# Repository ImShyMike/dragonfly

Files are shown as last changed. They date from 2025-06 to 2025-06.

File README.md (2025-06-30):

# dragonfly

A tiny 3.5" FPV drone for [highway](https://highway.hackclub.com) with a fully custom frame, corners, softmounts and ELRS receiver.

I've seen many FPV videos and always thought that it was really cool. Only issue is that I only own a small toy drone without a camera.

When highway released I thought it would be a great oportunity to learn what goes into designing your own FPV drone. After alot of research I managed to make a decent looking frame and find parts that could keep the cost reasonably low.

---

## Render

Model render

<sub>The model with sample props, motors and camera (along with a 15cm ruler for scale).</sub>

Custom ELRS PCB render

---

## BOM

| Part | Qty | Price (USD) | Link |
| --- | :-: | :---: | --- |
| SpeedyBee F405 Mini BLS 35A 20×20 Stack  |  1  | 60.00 | [https://www.speedybee.com/speedybee-f405-mini-bls-35a-20x20-stack](https://www.speedybee.com/speedybee-f405-mini-bls-35a-20x20-stack) |
| 20 mm Aluminum Standoffs (pack) |  1  | 1.86 | [https://pt.aliexpress.com/item/1005007945167923.html](https://pt.aliexpress.com/item/1005007945167923.html) |
| HQProp 3525 Prop Set |  1  | 3.31 | [https://pt.aliexpress.com/item/1005008744409414.html](https://pt.aliexpress.com/item/1005008744409414.html) |
| CADDX ANT Camera |  1  | 13.98 | [https://pt.aliexpress.com/item/1005006086694992.html](https://pt.aliexpress.com/item/1005006086694992.html) |
| Omnidirectional Antenna Pair |  1  | 2.46 | [https://pt.aliexpress.com/item/1005007126266614.html](https://pt.aliexpress.com/item/1005007126266614.html) |
| YSIDO 1505 2650KV Brushless Motor Set |  1  | 29.11 | [https://pt.aliexpress.com/item/1005007544080274.html](https://pt.aliexpress.com/item/1005007544080274.html) |
| HGLRC Zeus Nano VTX |  1  | 22.96 | [https://pt.aliexpress.com/item/1005008043478143.html](https://pt.aliexpress.com/item/1005008043478143.html) |
| Mini RHCP 5.8 GHz Lollipop Antenna (UFL) |  1  | 5.34 | [https://pt.aliexpress.com/item/4001365632031.html](https://pt.aliexpress.com/item/4001365632031.html) |
| **Total** | |  **139.02** | |

The current price of the ELRS receiver is 69.60$ and using the cheapest shipping the total is at 215.91$.

The BOM does not account for the frame and battery as I couldn't get that under 150$ D:

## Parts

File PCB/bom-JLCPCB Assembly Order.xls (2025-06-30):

JLCPCB BOM Tool - BOM Matching
BOM name：bom-JLCPCB Assembly Order.xlsx |  |  | Download Time：2025-06-25 01:11:42 |  |  |  | * Our matching results are updated in real-time, but stock and prices may change. If it's been over 24 hours, please re-match before placing your order.
PCB Assembled Qty：5 |  |  | Est. Total Price：20.4626
Your BOM |  |  |  |  | Matched Parts |  |  |  |  |  |  | Order Information
Top Designator | Bottom Designator | Comment | Footprint | JLCPCB Part # | Matches | Part # | Manufacturer | Footprint | Description | Category | Warning | JLCPCB Part # | Product link | Lib Type | Qty | Source | Total Price ($)
C1 |  | 25V1uF | 0402 |  | Unconfirmed | CL05A105KA5NQNC | Samsung Electro-Mechanics | 0402 | 25V 1uF X5R ±10% 0402 Multilayer Ceramic Capacitors MLCC - SMD/SMT ROHS | Multilayer Ceramic Capacitors MLCC - SMD/SMT | 1.The comment (CL05A105KA5NQNC) of this part does not match the one (25V1uF) provided in your BOM. Please confirm; 2.Multiple lines in the BOM have been matched to the same part. Please check if the matching is correct. ; | C52923 | https://jlcpcb.com/partdetail/53938-CL05A105KA5NQNC/C52923 | Basic | 6 | 6 JLCPCB | 0.018
C11 |  | 1uF25v | 0402 |  | Unconfirmed | CL05A105KA5NQNC | Samsung Electro-Mechanics | 0402 | 25V 1uF X5R ±10% 0402 Multilayer Ceramic Capacitors MLCC - SMD/SMT ROHS | Multilayer Ceramic Capacitors MLCC - SMD/SMT | 1.Multiple lines in the BOM have been matched to the same part. Please check if the matching is correct. ; | C52923 | https://jlcpcb.com/partdetail/53938-CL05A105KA5NQNC/C52923 | Basic | 6 | 6 JLCPCB | 0.018
C12 |  | 1uF | 0402 |  | Unconfirmed | CL05A105KA5NQNC | Samsung Electro-Mechanics | 0402 | 25V 1uF X5R ±10% 0402 Multilayer Ceramic Capacitors MLCC - SMD/SMT ROHS | Multilayer Ceramic Capacitors MLCC - SMD/SMT | 1.Multiple lines in the BOM have been matched to the same part. Please check if the matching is correct. ; | C52923 | https://jlcpcb.com/partdetail/53938-CL05A105KA5NQNC/C52923 | Basic | 6 | 6 JLCPCB | 0.018
C2 |  | 470nF,10V | 0402 |  | Select by System | CL05A474KP5NNNC | Samsung Electro-Mechanics | 0402 | 10V 470nF X5R ±10% 0402 Multilayer Ceramic Capacitors MLCC - SMD/SMT ROHS | Multilayer Ceramic Capacitors MLCC - SMD/SMT |  | C47339 | https://jlcpcb.com/partdetail/48344-CL05A474KP5NNNC/C47339 | Extended | 20 | 20 JLCPCB | 0.066
C3 |  | 10nF | 0402 |  | Select by System | CL05B103KB5NNNC | Samsung Electro-Mechanics | 0402 | 50V 10nF X7R ±10% 0402 Multilayer Ceramic Capacitors MLCC - SMD/SMT ROHS | Multilayer Ceramic Capacitors MLCC - SMD/SMT |  | C15195 | https://jlcpcb.com/partdetail/15869-CL05B103KB5NNNC/C15195 | Basic | 4 | 4 JLCPCB | 0.0052
C8 |  | 10nF | 0402 |  | Select by System | CL05B103KB5NNNC | Samsung Electro-Mechanics | 0402 | 50V 10nF X7R ±10% 0402 Multilayer Ceramic Capacitors MLCC - SMD/SMT ROHS | Multilayer Ceramic Capacitors MLCC - SMD/SMT |  | C15195 | https://jlcpcb.com/partdetail/15869-CL05B103KB5NNNC/C15195 | Basic | 4 | 4 JLCPCB | 0.0052
C4 |  | 10uF | 0402 |  | Select by System | CL05A106MQ5NUNC | Samsung Electro-Mechanics | 0402 | 6.3V 10uF X5R ±20% 0402 Multilayer Ceramic Capacitors MLCC - SMD/SMT ROHS | Multilayer Ceramic Capacitors MLCC - SMD/SMT |  | C15525 | https://jlcpcb.com/partdetail/16204-CL05A106MQ5NUNC/C15525 | Basic | 2 | 2 JLCPCB | 0.0122
C6,C7 |  | 10pF | 0402 |  | Select by System | CL05C100JB5NNNC | Samsung Electro-Mechanics | 0402 | 50V 10pF C0G ±5% 0402 Multilayer Ceramic Capacitors MLCC - SMD/SMT ROHS | Multilayer Ceramic Capacitors MLCC - SMD/SMT |  | C32949 | https://jlcpcb.com/partdetail/33914-CL05C100JB5NNNC/C32949 | Basic | 8 | 8 JLCPCB | 0.0344
C17,C19 |  | 10pF | 0402 |  | Select by System | CL05C100JB5NNNC | Samsung Electro-Mechanics | 0402 | 50V 10pF C0G ±5% 0402 Multilayer Ceramic Capacitors MLCC - SMD/SMT ROHS | Multilayer Ceramic Capacitors MLCC - SMD/SMT |  | C32949 | https://jlcpcb.com/partdetail/33914-CL05C100JB5NNNC/C32949 | Basic | 8 | 8 JLCPCB | 0.0344
C10,C5,C9 |  | 100nF | 0402 |  | Select by System | CL05B104KO5NNNC | Samsung Electro-Mechanics | 0402 | 16V 100nF X7R ±10% 0402 Multilayer Ceramic Capacitors MLCC - SMD/SMT ROHS | Multilayer Ceramic Capacitors MLCC - SMD/SMT |  | C1525 | https://jlcpcb.com/partdetail/1877-CL05B104KO5NNNC/C1525 | Basic | 8 | 8 JLCPCB | 0.0088
C18 |  | 100nF | 0402 |  | Select by System | CL05B104KO5NNNC | Samsung Electro-Mechanics | 0402 | 16V 100nF X7R ±10% 0402 Multilayer Ceramic Capacitors MLCC - SMD/SMT ROHS | Multilayer Ceramic Capacitors MLCC - SMD/SMT |  | C1525 | https://jlcpcb.com/partdetail/1877-CL05B104KO5NNNC/C1525 | Basic | 8 | 8 JLCPCB | 0.0088
C13 |  | 2.2uF | 0402 |  | Select by Customer | CL05A225MQ5NSNC | Samsung Electro-Mechanics | 0402 | 6.3V 2.2uF X5R ±20% 0402 Multilayer Ceramic Capacitors MLCC - SMD/SMT ROHS | Multilayer Ceramic Capacitors MLCC - SMD/SMT |  | C12530 | https://jlcpcb.com/partdetail/13164-CL05A225MQ5NSNC/C12530 | Basic | 2 | 2 JLCPCB | 0.0048
C14,C15,C16,C20 |  | 1.2pF | 0402 |  | Select by System | CC0402BRNPO9BN1R2 | YAGEO | 0402 | 50V 1.2pF NP0 0402 Multilayer Ceramic Capacitors MLCC - SMD/SMT ROHS | Multilayer Ceramic Capacitors MLCC - SMD/SMT |  | C327292 | https://jlcpcb.com/partdetail/YAGEO-CC0402BRNPO9BN1R2/C327292 | Extended | 20 | 20 JLCPCB | 0.044
CN1,CN2 |  | Conn_Coaxial | U.FL_Hirose_U.FL-R-SMT-1_Vertical |  | Select by System | U.FL-R-SMT-1(80) | HRS(Hirose) | SMD | 1 Inner pin IPEX Board-End 1.25mm -40℃~+90℃ 6GHz 50Ω 2mm SMD Coaxial Connectors (RF) ROHS | Coaxial Connectors (RF) |  | C88374 | https://jlcpcb.com/partdetail/HRS_Hirose-U_FL_R_SMT_1_80/C88374 | Extended | 6 | 6 JLCPCB | 0.5556
D1 |  | LED | 0603 |  | Select by System | KT-0603R | Hubei KENTO Elec | 0603 | -40℃~+85℃ Red 0603 LED Indication - Discrete ROHS | LED Indication - Discrete |  | C2286 | https://jlcpcb.com/partdetail/Hubei_KENTOElec-KT0603R/C2286 | Basic | 2 | 2 JLCPCB | 0.0112
L1 |  | 15u | 0805 |  | Select by System | MGFL2012F150MT-LF | microgate | 0805 | 400mA 15uH ±20% 500mΩ 0805 Inductors (SMD) ROHS | Inductors (SMD) |  | C486333 | https://jlcpcb.com/partdetail/microgate-MGFL2012F150MTLF/C486333 | Extended | 6 | 6 JLCPCB | 0.2088
L2,L3 |  | 3n | 0402 |  | Select by System | LQW15AN3N0B00D | Murata Electronics | 0402 | 750mA 3nH 0402 Power Inductors ROHS | Power Inductors |  | C269824 | https://jlcpcb.com/partdetail/MurataElectronics-LQW15AN3N0B00D/C269824 | Extended | 8 | 8 JLCPCB | 0.2584
LDO1 |  | AMS1117 | SOT-223-3_TabPin2 |  | Select by Customer | AMS1117-3.3 | Advanced Monolithic Systems | SOT-223 | 72dB@(120Hz) 1A Fixed 3.3V Positive electrode SOT-223 Voltage Regulators - Linear, Low Drop Out (LDO) Regulators ROHS | Voltage Regulators - Linear, Low Drop Out (LDO) Regulators |  | C6186 | https://jlcpcb.com/partdetail/Advanced_MonolithicSystems-AMS1117_33/C6186 | Basic | 2 | 2 JLCPCB | 0.3408
R1,R2,R3,R4 |  | 10k | 0402 |  | Unconfirmed | 0402WGF1002TCE | UNI-ROYAL(Uniroyal Elec) | 0402 | 62.5mW Thick Film Resistors 50V ±100ppm/℃ ±1% 10kΩ 0402 Chip Resistor - Surface Mount ROHS | Chip Resistor - Surface Mount | 1.The comment (0402WGF1002TCE) of this part does not match the one (10k) provided in your BOM. Please confirm; | C25744 | https://jlcpcb.com/partdetail/26487-0402WGF1002TCE/C25744 | Basic | 8 | 8 JLCPCB | 0.004
R5 |  | 3.3k | 0402 |  | Select by System | 0402WGF3301TCE | UNI-ROYAL(Uniroyal Elec) | 0402 | 62.5mW Thick Film Resistors 50V ±100ppm/℃ ±1% 3.3kΩ 0402 Chip Resistor - Surface Mount ROHS | Chip Resistor - Surface Mount |  | C25890 | https://jlcpcb.com/partdetail/26633-0402WGF3301TCE/C25890 | Basic | 2 | 2 JLCPCB | 0.001
R6 |  | 12k | 0402 |  | Select by System | 0402WGF1202TCE | UNI-ROYAL(Uniroyal Elec) | 0402 | 62.5mW Thick Film Resistors 50V ±100ppm/℃ ±1% 12kΩ 0402 Chip Resistor - Surface Mount ROHS | Chip Resistor - Surface Mount |  | C25752 | https://jlcpcb.com/partdetail/26495-0402WGF1202TCE/C25752 | Basic | 2 | 2 JLCPCB | 0.001
R7 |  | 2.2k | 0402 |  | Select by System | 0402WGF2201TCE | UNI-ROYAL(Uniroyal Elec) | 0402 | 62.5mW Thick Film Resistors 50V ±100ppm/℃ ±1% 2.2kΩ 0402 Chip Resistor - Surface Mount ROHS | Chip Resistor - Surface Mount |  | C25879 | https://jlcpcb.com/partdetail/26622-0402WGF2201TCE/C25879 | Basic | 2 | 2 JLCPCB | 0.001
R8 |  | 1.2k | 0402 |  | Select by System | 0402WGF1201TCE | UNI-ROYAL(Uniroyal Elec) | 0402 | 62.5mW Thick Film Resistors 50V ±100ppm/℃ ±1% 1.2kΩ 0402 Chip Resistor - Surface Mount ROHS | Chip Resistor - Surface Mount |  | C25862 | https://jlcpcb.com/partdetail/26605-0402WGF1201TCE/C25862 | Extended | 20 | 20 JLCPCB | 0.01
R9 |  | 100k | 0402 |  | Select by System | 0402WGF1003TCE | UNI-ROYAL(Uniroyal Elec) | 0402 | 62.5mW Thick Film Resistors 50V ±100ppm/℃ ±1% 100kΩ 0402 Chip Resistor - Surface Mount ROHS | Chip Resistor - Surface Mount |  | C25741 | https://jlcpcb.com/partdetail/26484-0402WGF1003TCE/C25741 | Basic | 2 | 2 JLCPCB | 0.001
SW1 |  | SW_Push | SW_SPST_B3U-1000P-B |  | Select by Customer | B3U-1000P | Omron Electronics | SMD,2.5x3mm | 2.5mm 1.6mm Round Button 50mA Standing paste 3mm SPST 153gf 12V SMD,2.5x3mm Tactile Switches ROHS | Tactile Switches |  | C231329 | https://jlcpcb.com/partdetail/OmronElectronics-B3U1000P/C231329 | Extended | 5 | 5 JLCPCB | 0.7645
U1 |  | ESP8285 | QFN-32-1EP_5x5mm_P0.5mm_EP3.45x3.45mm |  | Select by Customer | ESP8285N08 | Espressif Systems | QFN-32-EP(5x5) | 72.2Mbps 2.4GHz~2.483GHz ADC,GPIO,I2C,I2S,PWM,SDIO,SPI,UART QFN-32-EP(5x5) RF Transceiver ICs ROHS | RF Transceiver ICs | 1.The comment (ESP8285N08) of this part does not match the one (ESP8285) provided in your BOM. Please confirm; | C967018 | https://jlcpcb.com/partdetail/EspressifSystems-ESP8285N08/C967018 | Extended | 2 | 2 JLCPCB | 1.86
U2 |  | SX1280IMLTRT | XCVR_SX1280IMLTRT |  | Select by System | SX1280IMLTRT | SEMTECH | QFN-24-EP(4x4) | 802.15.4 2.4GHz SPI,UART QFN-24-EP(4x4) RF Transceiver ICs ROHS | RF Transceiver ICs |  | C125969 | https://jlcpcb.com/partdetail/SEMTECH-SX1280IMLTRT/C125969 | Extended | 2 | 2 JLCPCB | 8.955
U3 |  | SE2431L-R | SE2431L_SKY |  | Select by System | SE2431L-R | Skyworks Solutions | QFN-24-EP(3x4) | QFN-24-EP(3x4) RF Amplifiers ROHS | RF Amplifiers |  | C2649471 | https://jlcpcb.com/partdetail/SkyworksSolutions-SE2431LR/C2649471 | Extended | 2 | 2 JLCPCB | 5.694
U4 |  | DEA142450BT-3024A1 | RF_3024A1_TDK |  | Select by System | DEA142450BT-3024A1 | TDK | SMD,1.1x1.4mm | SMD,1.1x1.4mm RF Filters ROHS | RF Filters |  | C695577 | https://jlcpcb.com/partdetail/TDK-DEA142450BT3024A1/C695577 | Extended | 5 | 5 JLCPCB | 0.415
Y1 |  | 26Mhz | Crystal_SMD_2016-4Pin_2.0x1.6mm |  | Select by Customer | X201626MLB4SI | YXC Crystal Oscillators | SMD2016-4P | 26MHz SMD crystal oscillator 9pF ±10ppm ±20ppm SMD2016-4P Crystals ROHS | Crystals |  | C5210657 | https://jlcpcb.com/partdetail/5904004-X201626MLB4SI/C5210657 | Extended | 5 | 5 JLCPCB | 0.441
Y2 |  | 52Mhz,8pF | Crystal_SMD_2016-4Pin_2.0x1.6mm |  | Select by System | 7D052000F01 | HD | SMD2016-4P | 52MHz SMD crystal oscillator 8pF ±10ppm ±20ppm SMD2016-4P Crystals ROHS | Crystals |  | C781783 | https://jlcpcb.com/partdetail/HD-7D052000F01/C781783 | Extended | 5 | 5 JLCPCB | 0.6625

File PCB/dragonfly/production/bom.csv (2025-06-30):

Designator | Footprint | Quantity | Value | LCSC Part #
5V1, GND1, RX1, TX1 | TestPoint_Pad_2.5x2.5mm | 4 | Conn_01x01_Female
C1 | 0402 | 1 | 25V 1uF
C10, C5, C9 | 0402 | 3 | 100nF
C11 | 0402 | 1 | 1uF 25v | C52923
C12 | 0402 | 1 | 1uF | C52923
C13 | 0402 | 1 | 2.2uF | C52923
C14, C15, C16, C20 | 0402 | 4 | 1.2pF | C327292
C17, C19 | 0402 | 2 | 10pF | C32949
C18 | 0402 | 1 | 100nF | C1525
C2 | 0402 | 1 | 470nF, 10V | C47339
C3 | 0402 | 1 | 10nF | C15195
C4 | 0402 | 1 | 10uF
C6, C7 | 0402 | 2 | 10pF
C8 | 0402 | 1 | 10nF
CN1, CN2 | U.FL_Hirose_U.FL-R-SMT-1_Vertical | 2 | Conn_Coaxial | C88374
D1 | 0603 | 1 | LED | C2286
L1 | 0805 | 1 | 15u | C486333
L2, L3 | 0402 | 2 | 3n | C269824
LDO1 | SOT-223-3_TabPin2 | 1 | AMS1117
R1, R2, R3, R4 | 0402 | 4 | 10k
R5 | 0402 | 1 | 3.3k | C25890
R6 | 0402 | 1 | 12k | C25752
R7 | 0402 | 1 | 2.2k | C25879
R8 | 0402 | 1 | 1.2k | C25862
R9 | 0402 | 1 | 100k | C25741
SW1 | SW_SPST_B3U-1000P-B | 1 | SW_Push
U1 | QFN-32-1EP_5x5mm_P0.5mm_EP3.45x3.45mm | 1 | ESP8285
U2 | XCVR_SX1280IMLTRT | 1 | SX1280IMLTRT
U3 | SE2431L_SKY | 1 | SE2431L-R
U4 | RF_3024A1_TDK | 1 | DEA142450BT-3024A1
Y1 | Crystal_SMD_2016-4Pin_2.0x1.6mm | 1 | 26Mhz
Y2 | Crystal_SMD_2016-4Pin_2.0x1.6mm | 1 | 52Mhz, 8pF | C781783

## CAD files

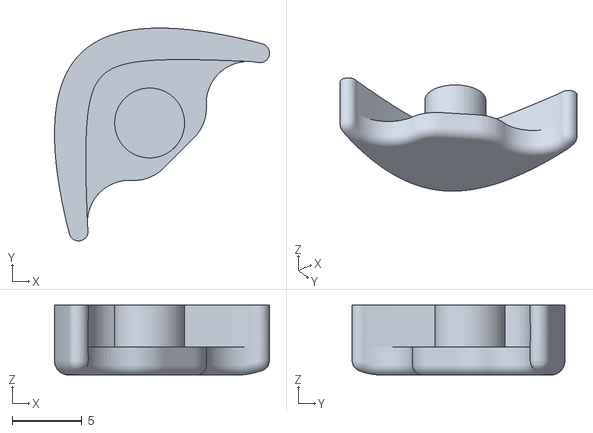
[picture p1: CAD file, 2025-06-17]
CAD/corner.stl
15.4 x 15.2 x 5.00

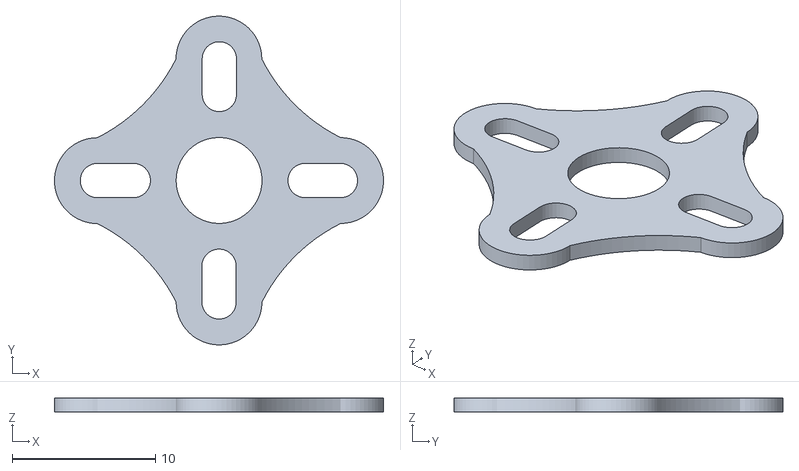
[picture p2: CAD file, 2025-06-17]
CAD/motor_softmount.stl
23.0 x 23.0 x 1.00

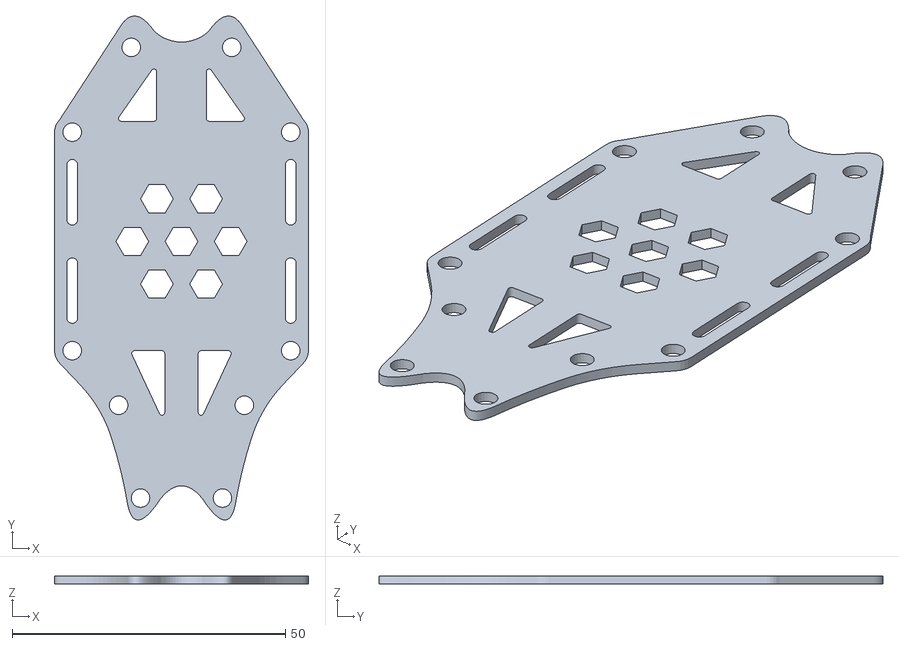
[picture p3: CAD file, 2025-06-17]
CAD/frame_top.stl
46.5 x 92.3 x 1.50

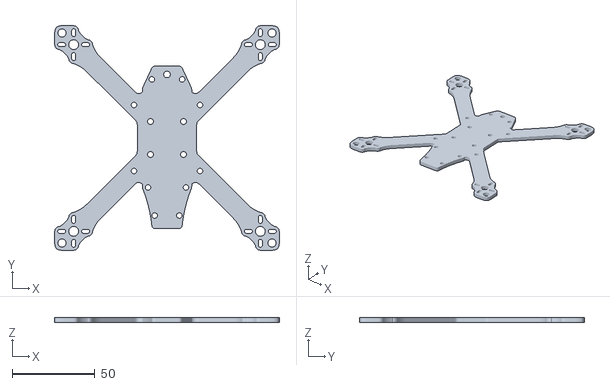
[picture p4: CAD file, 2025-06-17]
CAD/frame_body.stl
136.4 x 136.4 x 3.00

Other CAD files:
CAD/dragonfly.f3z

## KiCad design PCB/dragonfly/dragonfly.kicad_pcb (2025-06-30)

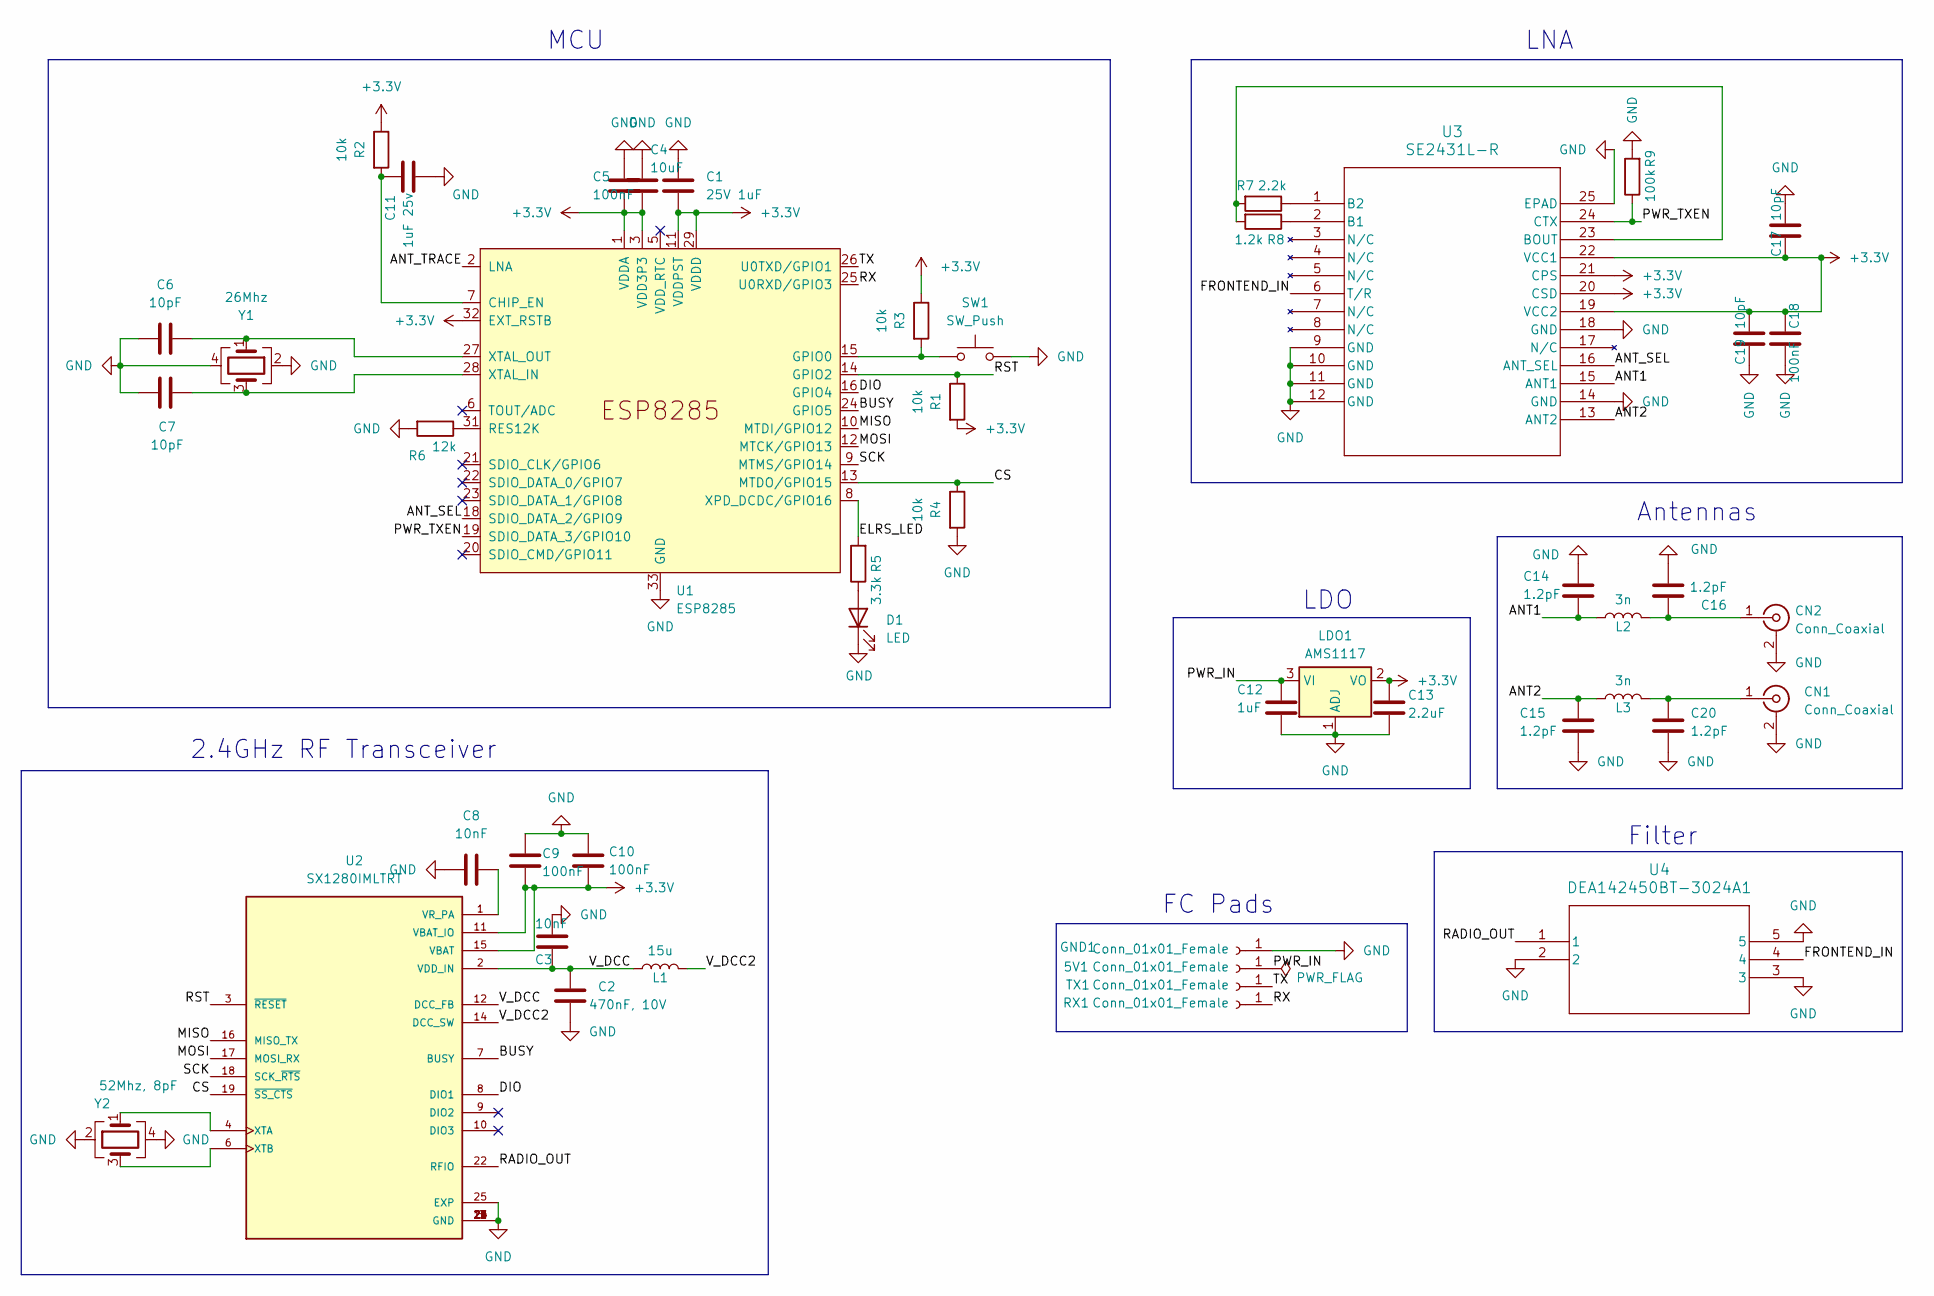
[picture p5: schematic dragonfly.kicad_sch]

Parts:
5V1: Conn_01x01_Female; TestPoint_Pad_2.5x2.5mm
C1: 25V 1uF; C_0402_1005Metric
C2: 470nF, 10V; C_0402_1005Metric; LCSC C47339
C3: 10nF; C_0402_1005Metric; LCSC C15195
C4: 10uF; C_0402_1005Metric
C5, C9, C10: 100nF; C_0402_1005Metric
C6, C7: 10pF; C_0402_1005Metric
C8: 10nF; C_0402_1005Metric
C11: 1uF 25v; C_0402_1005Metric; LCSC C52923
C12: 1uF; C_0402_1005Metric; LCSC C52923
C13: 2.2uF; C_0402_1005Metric; LCSC C52923
C14, C15, C16, C20: 1.2pF; C_0402_1005Metric; LCSC C327292
C17, C19: 10pF; C_0402_1005Metric; LCSC C32949
C18: 100nF; C_0402_1005Metric; LCSC C1525
CN1, CN2: Conn_Coaxial; U.FL_Hirose_U.FL-R-SMT-1_Vertical; Part Hirose U.FL-R-SMT-1(80); LCSC C88374
D1: LED; LED_0603_1608Metric; LCSC C2286
GND1: Conn_01x01_Female; TestPoint_Pad_2.5x2.5mm
L1: 15u; L_0805_2012Metric; LCSC C486333
L2, L3: 3n; L_0402_1005Metric; LCSC C269824
LDO1: AMS1117; SOT-223-3_TabPin2
R1, R2, R3, R4: 10k; R_0402_1005Metric
R5: 3.3k; R_0402_1005Metric; LCSC C25890
R6: 12k; R_0402_1005Metric; LCSC C25752
R7: 2.2k; R_0402_1005Metric; LCSC C25879
R8: 1.2k; R_0402_1005Metric; LCSC C25862
R9: 100k; R_0402_1005Metric; LCSC C25741
RX1: Conn_01x01_Female; TestPoint_Pad_2.5x2.5mm
SW1: SW_Push; SW_SPST_B3U-1000P-B
TX1: Conn_01x01_Female; TestPoint_Pad_2.5x2.5mm
U1: ESP8285; QFN-32-1EP_5x5mm_P0.5mm_EP3.45x3.45mm
U2: SX1280IMLTRT; XCVR_SX1280IMLTRT; PARTREV 3.3
U3: SE2431L-R; SE2431L_SKY
U4: DEA142450BT-3024A1; RF_3024A1_TDK
Y1: 26Mhz; Crystal_SMD_2016-4Pin_2.0x1.6mm
Y2: 52Mhz, 8pF; Crystal_SMD_2016-4Pin_2.0x1.6mm; LCSC C781783

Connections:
+3.3V: C1.2, C4.2, C5.1, C9.1, C10.1, C13.1, C17.2, C18.1, C19.1, LDO1.2 (VO), R1.2, R2.1, R3.1, U1.1 (VDDA), U1.3 (VDD3P3), U1.4 (VDD3P3), U1.11 (VDDPST), U1.17 (VDDPST), U1.29 (VDDD), U1.30 (VDDA), U1.32 (EXT_RSTB), U2.11 (VBAT_IO), U2.15 (VBAT), U3.19 (VCC2), U3.20 (CSD), U3.21 (CPS), U3.22 (VCC1)
/ANT1: C14.2, L2.1, U3.15 (ANT1)
/ANT2: C15.1, L3.1, U3.13 (ANT2)
/ANT_SEL: U1.18 (SDIO_DATA_2/GPIO9), U3.16 (ANT_SEL)
/ANT_TRACE: U1.2 (LNA)
/BUSY: U1.24 (GPIO5), U2.7 (BUSY)
/CS: R4.1, U1.13 (MTDO/GPIO15), U2.19 (~SS_CTS)
/DIO: U1.16 (GPIO4), U2.8 (DIO1)
/ELRS_LED: R5.2, U1.8 (XPD_DCDC/GPIO16)
/FRONTEND_IN: U3.6 (T/R), U4.4
/MISO: U1.10 (MTDI/GPIO12), U2.16 (MISO_TX)
/MOSI: U1.12 (MTCK/GPIO13), U2.17 (MOSI_RX)
/PWR_IN: 5V1.1, C12.1, LDO1.3 (VI)
/PWR_TXEN: R9.1, U1.19 (SDIO_DATA_3/GPIO10), U3.24 (CTX)
/RADIO_OUT: U2.22 (RFIO), U4.1
/RST: R1.1, U1.14 (GPIO2), U2.3 (~RESET)
/RX: RX1.1, U1.25 (U0RXD/GPIO3)
/SCK: U1.9 (MTMS/GPIO14), U2.18 (SCK_~RTS)
/TX: TX1.1, U1.26 (U0TXD/GPIO1)
/V_DCC: C2.1, C3.2, L1.1, U2.2 (VDD_IN), U2.12 (DCC_FB)
/V_DCC2: L1.2, U2.14 (DCC_SW)
GND: C1.1, C2.2, C3.1, C4.1, C5.2, C6.1, C7.1, C8.1, C9.2, C10.2, C11.2, C12.2, C13.2, C14.1, C15.2, C16.2, C17.1, C18.2, C19.2, C20.2, CN1.2 (Ext), CN2.2 (Ext), D1.1 (K), GND1.1, LDO1.1 (ADJ), R4.2, R6.2, R9.2, SW1.2, U1.33 (GND), U2.5 (GND), U2.13 (GND), U2.20 (GND), U2.21 (GND), U2.23 (GND), U2.24 (GND), U2.25 (EXP), U3.9 (GND), U3.10 (GND), U3.11 (GND), U3.12 (GND), U3.14 (GND), U3.18 (GND), U3.25 (EPAD), U4.2, U4.3, U4.5, Y1.2, Y1.4, Y2.2, Y2.4
unnamed: C20.1, CN1.1 (In), L3.2
unnamed: C16.1, CN2.1 (In), L2.2
unnamed: D1.2 (A), R5.1
unnamed: C11.1, R2.2, U1.7 (CHIP_EN)
unnamed: R3.2, SW1.1, U1.15 (GPIO0)
unnamed: R6.1, U1.31 (RES12K)
unnamed: C7.2, U1.28 (XTAL_IN), Y1.3
unnamed: C6.2, U1.27 (XTAL_OUT), Y1.1
unnamed: C8.2, U2.1 (VR_PA)
unnamed: U2.4 (XTA), Y2.1
unnamed: U2.6 (XTB), Y2.3
unnamed: R8.1, U3.2 (B1)
unnamed: R7.1, U3.1 (B2)
unnamed: R7.2, R8.2, U3.23 (BOUT)

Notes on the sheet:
Antennas
LNA
2.4GHz RF Transceiver
FC Pads
LDO
MCU
Filter

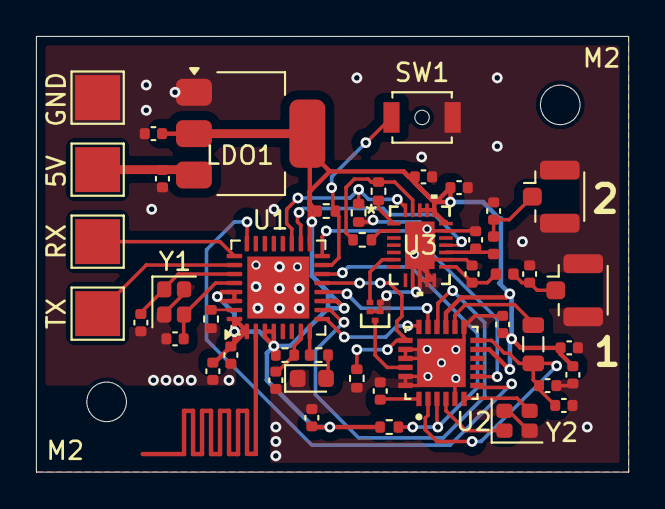
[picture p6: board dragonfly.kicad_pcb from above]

Board: 2 copper layers, 32.9 x 24.2 mm, 49 parts (0 on the bottom side), 35 nets.

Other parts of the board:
M2, M2#2: MountingHole_2.2mm_M2

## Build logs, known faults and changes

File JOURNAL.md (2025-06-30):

---
title: "dragonfly"
author: "ShyMike"
description: "Tiny 3.5" FPV drone with a fully custom frame"
created_at: "2025-06-13"
---

## Total time: 37h

---

# June 13th: Started researching

Started reading through [Drone Nodes's how to build a drone](https://dronenodes.com/how-to-build-a-drone) page and researching what components to use.

**Total time spent: 2h**

---

# June 13th pt2: Picked the main specifications (start of the frame)

This took way to much searching around but i think i've decided on the parts to use. (may be tweaked slightly)

* Class: 3.5-inch
* Frame size: 160mm
* Stack: 60$ - [SpeedyBee F405 Mini BLS 35A 20x20 Stack](https://www.speedybee.com/speedybee-f405-mini-bls-35a-20x20-stack)
* ~~VTX + Camera: 31.3$ - [Eachine TX06 700TVL](https://www.eachine.com/Eachine-TX06-700TVL-FOV-130-Degree-5_8Ghz-40CH-Smart-Audio-Mini-FPV-Camera-AIO-Transmitter-For-RC-Dr-p-1418.html)~~
* ~~VTX Antenna: 15.94$ -[Speedy Bee 5.8 GHz Antenna V2](https://www.speedybee.com/speedy-bee-5-8-ghz-antenna-v2)~~
* ~~Motors: 26.5$ - [Sparkhobby 1507 2700KV Brushless Motor](https://pt.aliexpress.com/item/1005004705279900.html)~~
* ~~ELRS Receiver: 10$ - [ELRS Nano Receiver](https://betafpv.com/products/elrs-nano-receiver?variant=39416095408262)~~
* Props: 8$ [Gemfan 3525](https://pt.aliexpress.com/item/1005008848979300.html)

Total: 151.74$

Also made the overall CAD layout for the frame :D

Frame CAD

**Total time spent: 6h**

---

# June 14th: Alot more CAD, repicked some stuff

After researching more turns out the other part wouldn't work so I picked something else.

* ~~Camera: 16$ - [CADDXFPV Ant Lite Analog Camera](https://caddxfpv.com/products/caddxfpv-ant-lite-4-3-fpvcycle-edition)~~
* ~~VTX: 35$ - [HappyModel OVX303](https://pt.aliexpress.com/item/1005003265460404.html)~~

Total: 154,5$

Also did more work on the frame:

Frame CAD 2

**Total time spent: 2h**

---

# June 14th pt2: Middle and top part

Remade the middle sketch because i used the wrong origin and it was off by about 0.01mm D:

Started working on the top part mounts.

Needed standoffs and switched to the camera version with actual mount spots D:

* Standoffs: 2.8$ - [20 mm Aluminum standoffs](https://pt.aliexpress.com/item/1005007945167923.html)
* Camera: 18$ - [CADDXFPV Ant Analog Camera](https://caddxfpv.com/products/caddx-ant-analog-camera?variant=32810079682659)

Total: 159,3$

Also made the near final version of the main body and made a WIP top part.

3D + standoffs
Top down with top part

**Total time spent: 5-6h**

---

# June 14th pt3: 3D model + finished top

Finished the top by adding all of the standoff and velcro holes.

Found some placeholder models for the camera and motors + props.

Full preview

Also thinking about a lolipop antenna:

* ~~VTX Antenna: 5$ - [Mini RHCP 5,8G Lollipop 4 antenna (Purple UFL Upgrade)](https://es.aliexpress.com/item/1005001305298735.html)~~

Total: 159,3$ - 164,3$

Added some space for the VTX antenna:

VTX antenna space

**Total time spent: 2h**

---

# June 15th: Finishing touches

Random list of stuff I might/will need so i don't forget it:

* Heat‑shrink
* 4S Battery pack
* Battery strap
* Threadlocker
* Buzzer
* Zip-ties

Made some TPU softmounts and corners and added some space at the front for the camera. Also smoothed out some rought corners and edges.

TPU softmounts + corners and front and rounded corners

**Total time spent: 2-3h**

---

# June 16th: Changed some stuff again

Found a cheaper and better VTX for the quad (along with a bunch of better parts for slightly more)

* VTX: 24$ - [HGLRC Zeus nano VTX](https://pt.aliexpress.com/item/1005008043478143.html) (just better and cheaper)
* Camera: 27.3$ - [Caddx Ratel 2 V2](https://pt.aliexpress.com/item/1005006254000307.html) (it's alot better but maybe slightly overkill)
* Motors: 30.6$ - [YSIDO 1505 2650KV](https://pt.aliexpress.com/item/1005007544080274.html) (the other motors were for 6S, not 4S and i somehow missed that)
* ELRS Receiver: 12.14$ - [BETAFPV ELRS Nano](https://pt.aliexpress.com/item/1005007437882037.html) (same receiver, saves money on shipping)
* VTX Antenna: 5.64$ - [Mini RHCP 5,8G Lollipop 4 antenna (Purple UFL Upgrade)](https://pt.aliexpress.com/item/4001365632031.html) (wrong website)

Total: 170.48$

**Total time spent: 2h**

---

# June 17th: Checking fabrication prices

> TIFO carbon fiber CNC is **_REALLY EXPENSIVE_** and would be over 50% of all other parts combined.

Checked the prices on PCBWay for carbon fiber and polycarbonate and I'm now waiting for the order review to know the actual price.

PCBWay order review

This is how the rendered version of the drone frame is looking now:

Rendered drone

(also spent way too long trying to export as a DXF from Fusion 360 but that requires a subcription so i had to do it using FreeCAD just to then realise that PCBWay uses step files, not DXF)

**Total time spent: 2h**

---

# June 18th: Sh!t, it's expensive

Just got the quotes and turns out getting it machined/3D printed won't be possible sadly :pensive-wobble: its wayyy outside of the 150$ budget :(

ITS EXPENSIVE :whyyy:

Will most likely have to try to get the frame/softmounts/corners from printing legion (as i don't own a 3D printer)

**TODO**: get the BOM under 150$ to fit in the 6 point middle tier (current BOM: 170.48$)

<sub>The current setup would need me to get the battery, battery straps and heatshrink myself, will see what i can do</sub>

**Total time spent: 1h**

---

# June 20th: The end (maybe)

> IT'S UNDER 150$!!!

Rechecked the price on everything and changed the camera back to the old one (much worse low ligth performance but the only way to fit the budget) and it's now under 150$ :yay: (excluding the frame :sob:)

* Props: 3.31$ - [2 Pairs HQProp 3525](https://pt.aliexpress.com/item/1005008744409414.html)
* Camera: 13.98$ - [CADDXFPV Baby Ratel2 Analog Camera](https://pt.aliexpress.com/item/1005006086694992.html)

Also double checked all the parts and they all currently have free shipping :p

**Total time spent: 2h**

---

# June 23th: ELRS receiver

> :sob:

Did not get aproved, ELRS receiver making moment (~~i love RF~~)

Rev 1

(based on the BETAFPV ELRS Nano Receiver)

**Total time spent: 5h**

# June 24th: BOM changes + ELRS stuff

Finished the ELRS PCB

Finished PCB render
Finished PCB schematic

Also changed the BOM:

* Antenna: 2.46$ - [Omnidirectional Antenna Pair](https://pt.aliexpress.com/item/1005007126266614.html)

**Total time spent: 4h**

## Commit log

2025-06-17 BOM :yay:
2025-06-17 add CAD
    [corner.stl, frame_body.stl, frame_top.stl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]
2025-06-20 IT'S UNDER 150$!!!!
    [BOM.csv]
2025-06-24 custom ELRS receiver :3
    [BOM.csv, bom.csv, designators.csv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]
2025-06-24 JLCPCB BOM
    [bom-JLCPCB Assembly Order.xls]
